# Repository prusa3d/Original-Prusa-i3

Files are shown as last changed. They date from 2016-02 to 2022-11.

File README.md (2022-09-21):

# Original Prusa i3 MK3S

Original Prusa i3 MK3S is a 3D printer project maintained by PRUSA RESEARCH.
Originates in [RepRap](https://reprap.org) project made possible by Dr. Adrian Bowyer and contributors.

This repository contains SCAD files and STLs of the printed parts.

**Links**

 * Prusa Research website : http://prusa3d.com
 * Product page: https://shop.prusa3d.com/en/3d-printers/180-original-prusa-i3-mk3-kit.html
 * Build manual: http://manual.prusa3d.com/c/Original_Prusa_i3_MK3_kit_assembly
 * Firmware : https://github.com/prusa3d/Prusa-Firmware
 * MK52 heatbed : https://github.com/prusa3d/Heatbed_MK52_magnetic
 * MK3 Power panic : https://github.com/prusa3d/MK3_Power_Panic
 * MK3S IR senzor : https://github.com/prusa3d/MKxS-IR-sensor

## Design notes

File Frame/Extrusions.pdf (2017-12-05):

## Profile

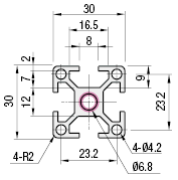
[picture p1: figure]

## Tapping

All 4.2 mm holes (both sides) tap 20 mm deep with M5

## Lengths

2x 205 mm : PAR-HWR-MK3-3030-205 2x 120 mm : PAR-HWR-MK3-3030-120

## Tolerance

+- 0.15 mm in length

# Material

Type: EN AC-51400-T5 Equiv. Surface finish: Black anodize

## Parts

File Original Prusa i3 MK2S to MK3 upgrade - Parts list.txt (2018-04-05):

Original Prusa i3 MK2S to Original Prusa i3 MK3 upgrade

Recommended print settings:
0.2 mm layer height, infill 20% GRID and material PETG.

Orange parts bundle (parts can be also printed in black):
X-end-motor (1x)	https://raw.githubusercontent.com/prusa3d/Original-Prusa-i3/MK3/Printed-Parts/stl/x-end-motor.stl
X-end-idler (1x)	https://raw.githubusercontent.com/prusa3d/Original-Prusa-i3/MK3/Printed-Parts/stl/x-end-idler.stl
Y-rod-holder (4x)	https://raw.githubusercontent.com/prusa3d/Original-Prusa-i3/MK3/Printed-Parts/stl/y-rod-holder.stl
Y-motor-holder (1x)	https://raw.githubusercontent.com/prusa3d/Original-Prusa-i3/MK3/Printed-Parts/stl/y-motor-holder.stl
Y-belt-holder (1x)	https://raw.githubusercontent.com/prusa3d/Original-Prusa-i3/MK3/Printed-Parts/stl/y-belt-holder.stl
Y-belt-idler (1x)	https://raw.githubusercontent.com/prusa3d/Original-Prusa-i3/MK3/Printed-Parts/stl/y-belt-idler.stl
Z-axis-top (1x) 	https://raw.githubusercontent.com/prusa3d/Original-Prusa-i3/MK3/Printed-Parts/stl/z-axis-top.stl
Z-axis-bottom (1x) 	https://raw.githubusercontent.com/prusa3d/Original-Prusa-i3/MK3/Printed-Parts/stl/z-axis-bottom.stl
LCD-supports (1x)	https://raw.githubusercontent.com/prusa3d/Original-Prusa-i3/MK3/Printed-Parts/stl/lcd-supports.stl

Black parts bundle (*extruder parts MUST BE printed in BLACK):
X-carriage* (1x)		https://raw.githubusercontent.com/prusa3d/Original-Prusa-i3/MK3/Printed-Parts/stl/x-carriage.stl
X-carriage-back* (1x)		https://raw.githubusercontent.com/prusa3d/Original-Prusa-i3/MK3/Printed-Parts/stl/x-carriage-back.stl     
Cable-holder* (1x)		https://raw.githubusercontent.com/prusa3d/Original-Prusa-i3/MK3/Printed-Parts/stl/cable-holder.stl
Extruder-body* (1x)		https://raw.githubusercontent.com/prusa3d/Original-Prusa-i3/MK3/Printed-Parts/stl/extruder-body.stl
Extruder-cover* (1x)		https://raw.githubusercontent.com/prusa3d/Original-Prusa-i3/MK3/Printed-Parts/stl/extruder-cover.stl
Extruder-idler-plug* (1x)	https://raw.githubusercontent.com/prusa3d/Original-Prusa-i3/MK3/Printed-Parts/stl/extruder-idler-plug.stl
Extruder-idler* (1x)		https://raw.githubusercontent.com/prusa3d/Original-Prusa-i3/MK3/Printed-Parts/stl/extruder-idler.stl
Filament-sensor-cover* (1x)	https://raw.githubusercontent.com/prusa3d/Original-Prusa-i3/MK3/Printed-Parts/stl/filament-sensor-cover.stl
Heatbed-cable-cover (1x)	https://raw.githubusercontent.com/prusa3d/Original-Prusa-i3/MK3/Printed-Parts/stl/heatbed-cable-cover.stl
Einsy-base (1x)			https://raw.githubusercontent.com/prusa3d/Original-Prusa-i3/MK3/Printed-Parts/stl/Einsy-base.stl
Einsy-doors (1x)		https://raw.githubusercontent.com/prusa3d/Original-Prusa-i3/MK3/Printed-Parts/stl/Einsy-doors.stl
Einsy-hinges (1x) 		https://raw.githubusercontent.com/prusa3d/Original-Prusa-i3/MK3/Printed-Parts/stl/Einsy-hinges.stl

License GNU GPL v3
https://www.prusa3d.com/prusa-i3-printable-parts/

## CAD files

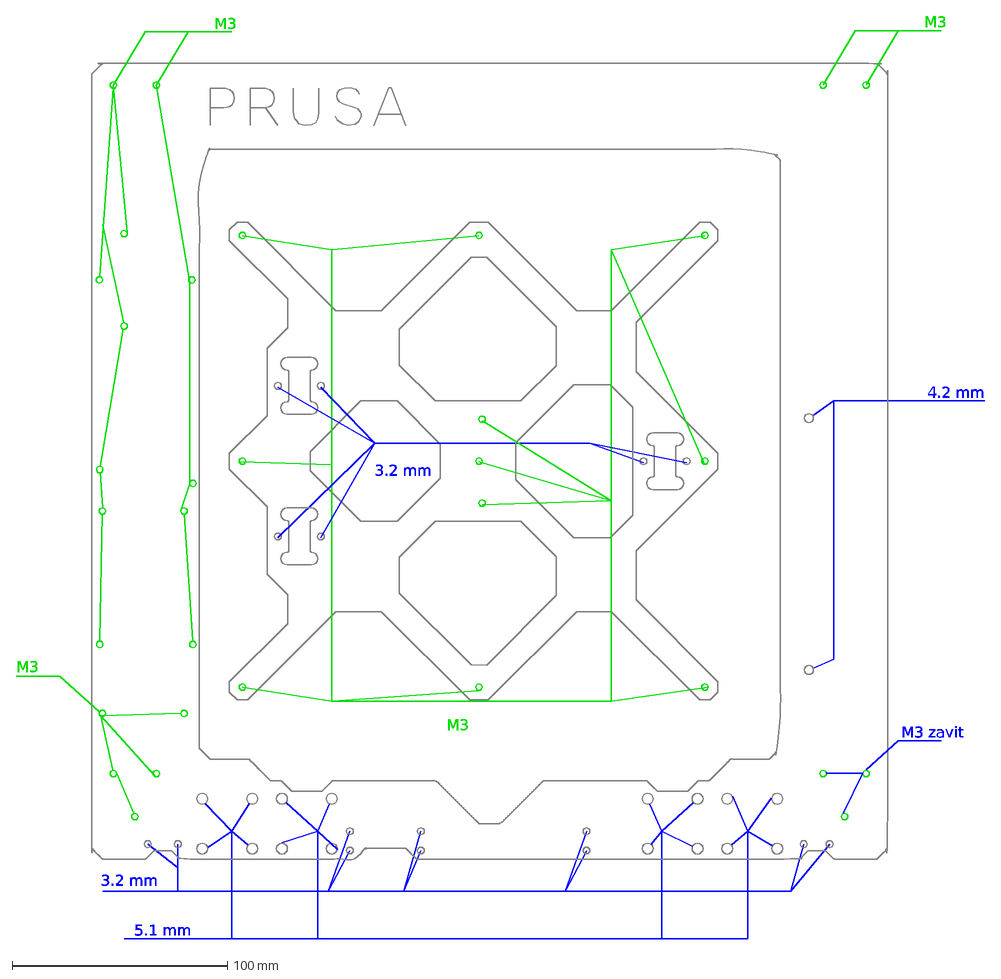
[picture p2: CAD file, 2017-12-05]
Frame/MK3v8b.dxf
4.2 mm
5.1 mm
M3
3.2 mm
M3 zavit

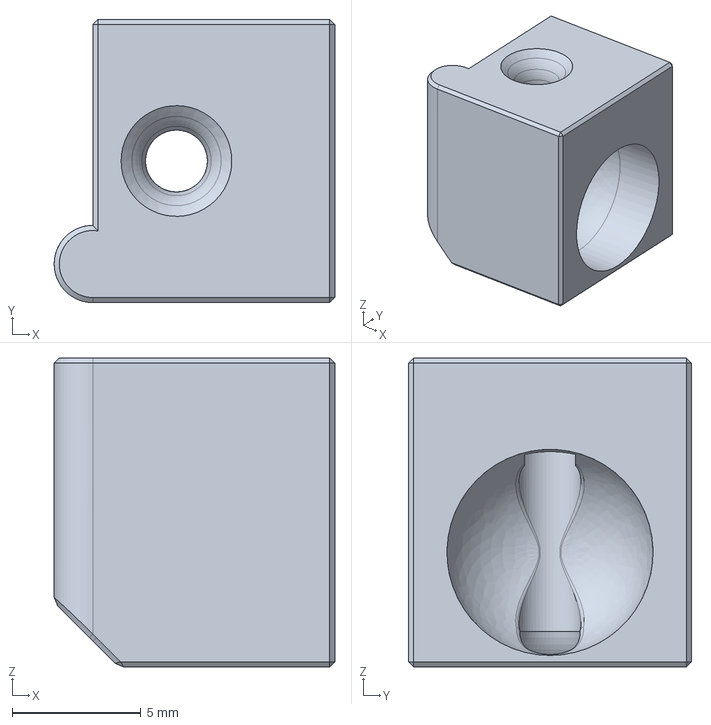
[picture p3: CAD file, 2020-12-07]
Printed-Parts/STEP/adapter-printer.stp
10.9 x 11.0 x 12.0 mm

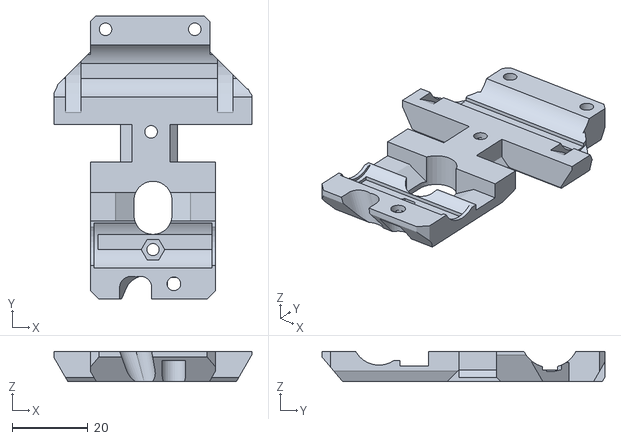
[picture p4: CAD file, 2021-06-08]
Printed-Parts/STL/x-carriage-back.stl
52.0 x 74.5 x 8.00

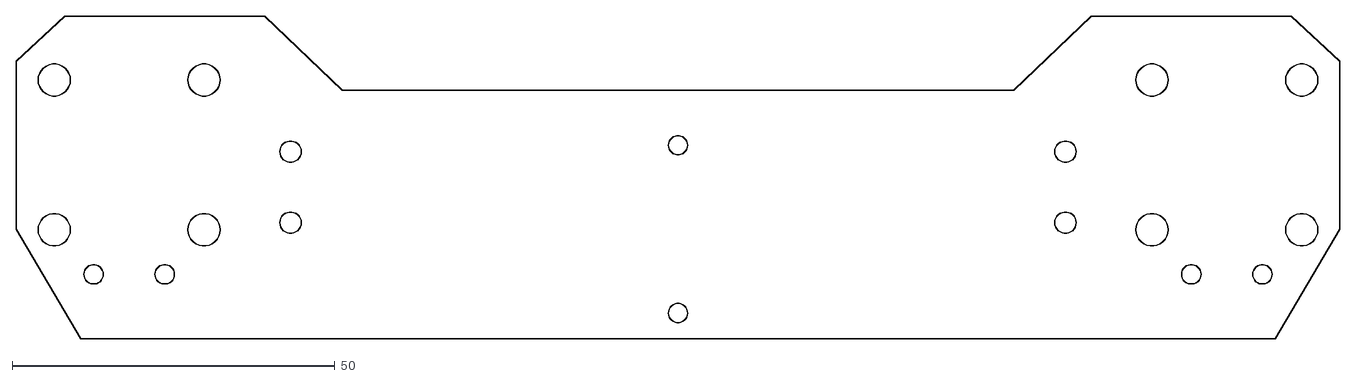
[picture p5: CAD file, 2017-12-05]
Frame/MK3-front-plate.dxf
205.0 x 50.0

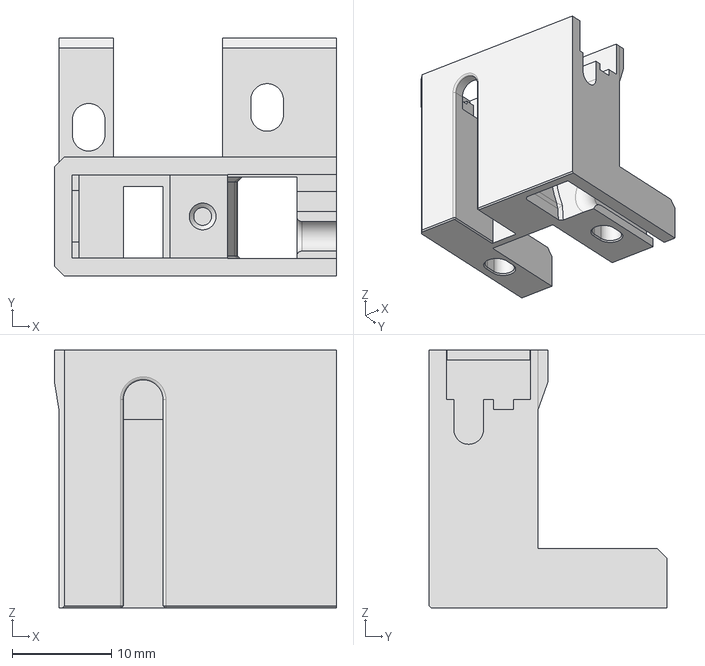
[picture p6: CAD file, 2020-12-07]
Printed-Parts/STEP/ir-sensor-holder-mmu2s.stp
28.5 x 24.0 x 26.0 mm

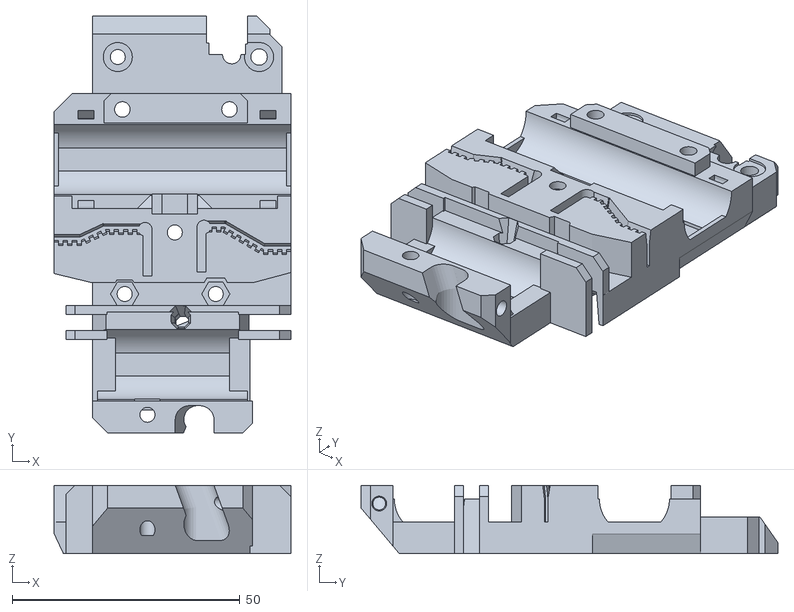
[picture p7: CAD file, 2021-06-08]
Printed-Parts/STL/x-carriage.stl
52.0 x 91.5 x 15.0

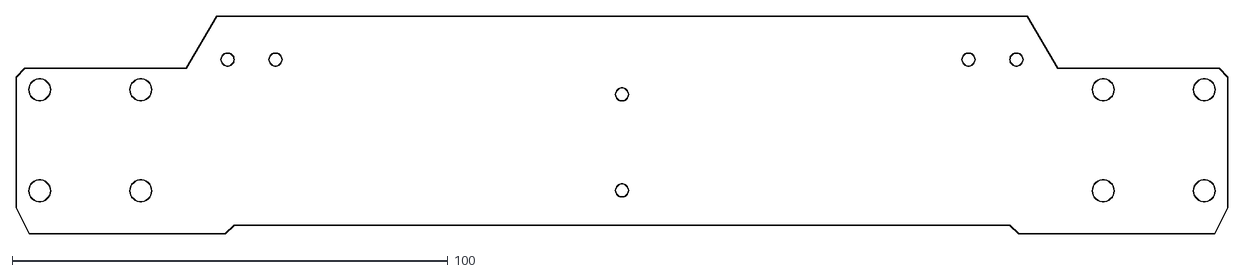
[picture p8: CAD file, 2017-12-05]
Frame/MK3-rear-plate.dxf
278.0 x 50.0

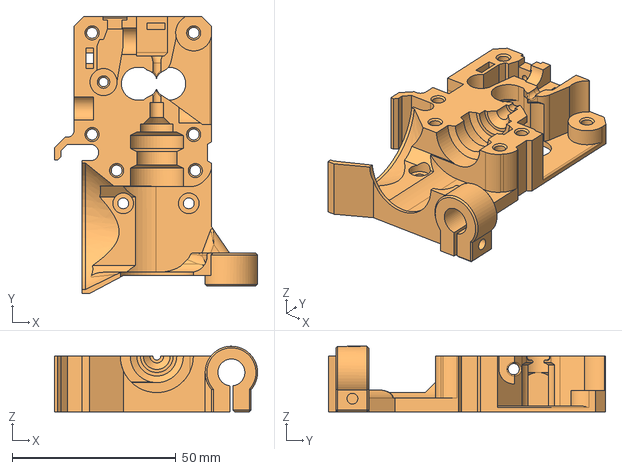
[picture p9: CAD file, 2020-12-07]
Printed-Parts/STEP/extruder-body.stp
62.0 x 84.5 x 20.0 mm

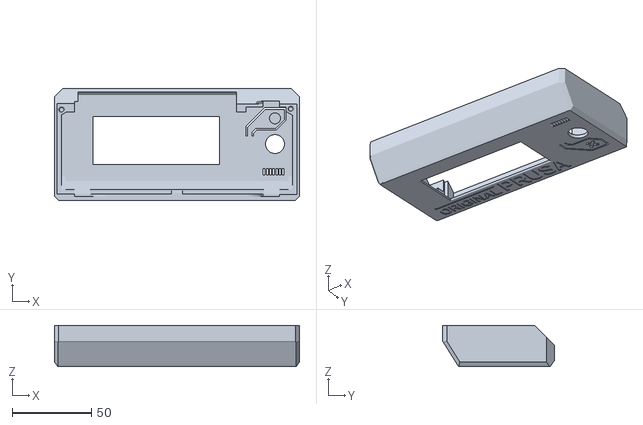
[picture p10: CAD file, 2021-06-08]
Printed-Parts/STL/LCD-cover-ORIGINAL-MK3.stl
155.0 x 70.7 x 26.0

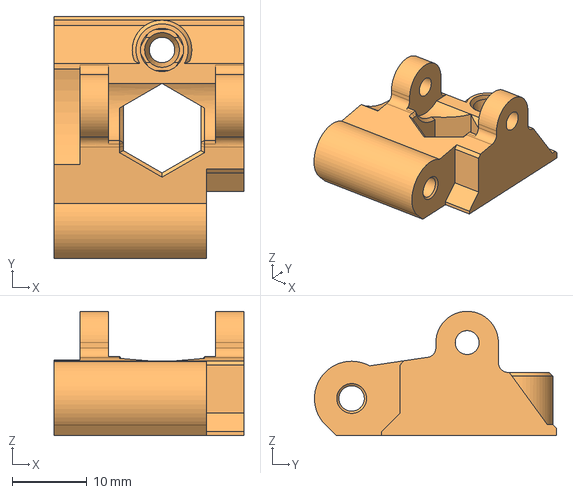
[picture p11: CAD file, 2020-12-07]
Printed-Parts/STEP/extruder-idler.stp
25.5 x 32.5 x 16.7 mm

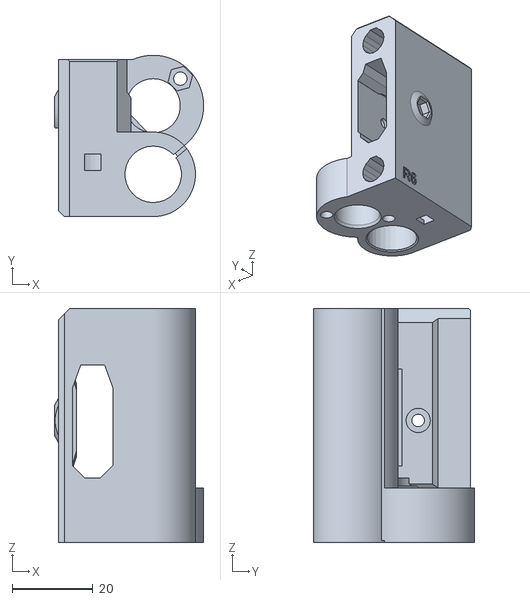
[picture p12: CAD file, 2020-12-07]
Printed-Parts/STL/x-end-idler.stl
37.0 x 40.0 x 58.0

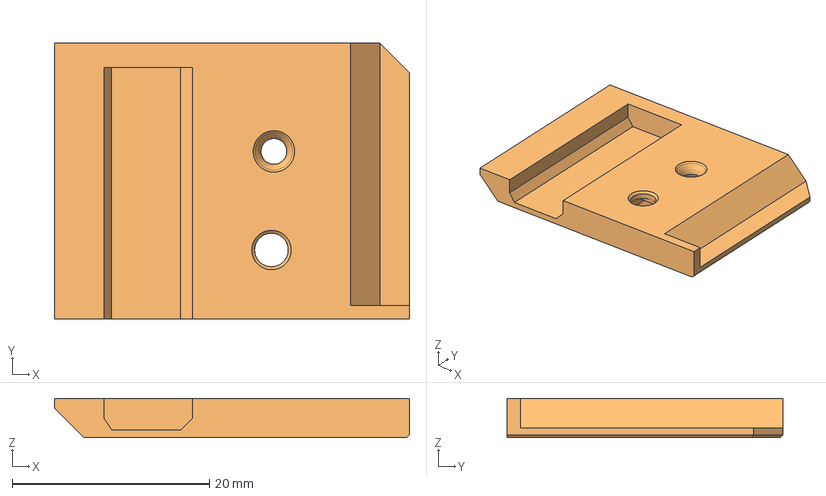
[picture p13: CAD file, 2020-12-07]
Printed-Parts/STEP/fs-cover.stp
36.0 x 28.0 x 4.00 mm

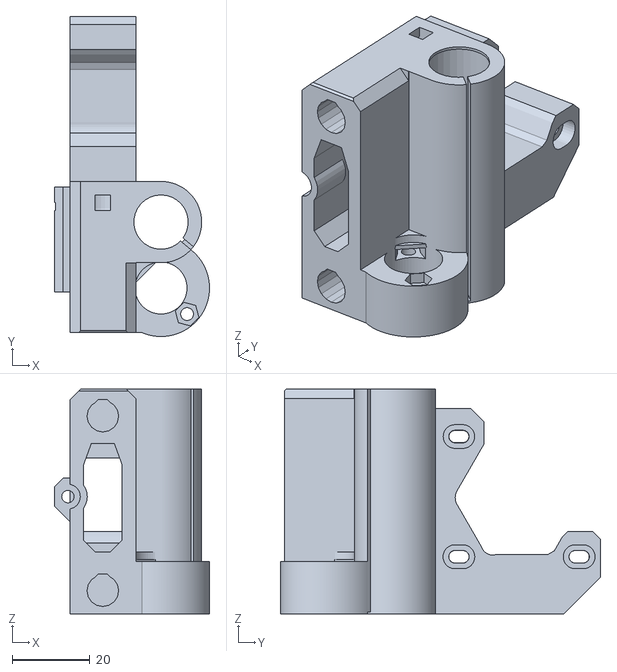
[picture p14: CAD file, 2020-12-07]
Printed-Parts/STL/x-end-motor.stl
40.0 x 82.5 x 58.0

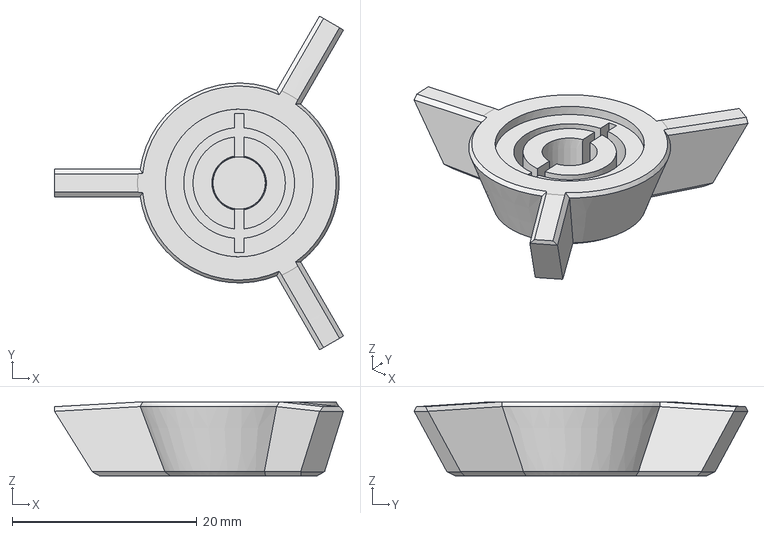
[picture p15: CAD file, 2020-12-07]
Printed-Parts/STEP/LCD-knob.stp
31.3 x 36.1 x 8.00 mm

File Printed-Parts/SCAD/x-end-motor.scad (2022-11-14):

// PRUSA iteration4
// X end motor
// GNU GPL v3
// Josef Průša <iam@josefprusa.cz> and contributors
// http://www.reprap.org/wiki/Prusa_Mendel
// http://prusamendel.org

use <x-end.scad>

module x_end_motor_base()
{
    x_end_base();
    translate(v=[-15,31,26.5]) cube(size = [17,44,53], center = true);

		
}

module x_end_motor_holes()
{
   x_end_holes();
    
    // Position to place
    translate(v=[-1,32,30.25])
    {
        // Belt hole
        translate(v=[-19,-21,-12]) cube(size = [10,25,22]);
        
        // Motor mounting holes

			for (x =[-1:0.25:1])
			{
        	translate(v=[0,-15.5+x,15.5]) rotate(a=[0,-90,0]) rotate(a=[0,0,90]) cylinder(h=30, r=1.55, $fn=60);
				translate(v=[0,-15.5+x,15.5]) rotate(a=[0,-90,0]) rotate(a=[0,0,90]) cylinder(h=18, r2=1.55, r1=1.7, $fn=60);
   	     translate(v=[1,-15.5+x,15.5]) rotate(a=[0,-90,0]) rotate(a=[0,0,90]) cylinder(h=10, r=3.05, $fn=60);
        
     	   	translate(v=[20,-15.5+x,-15.5]) rotate(a=[0,-90,0]) rotate(a=[0,0,90]) cylinder(h=70, r=1.6, $fn=30);
				translate(v=[0,-15.5+x,-15.5]) rotate(a=[0,-90,0]) rotate(a=[0,0,90]) cylinder(h=18, r2=1.55, r1=1.7, $fn=60);
     		  	translate(v=[1,-15.5+x,-15.5]) rotate(a=[0,-90,0]) rotate(a=[0,0,90]) cylinder(h=10, r=3.1, $fn=30);

	       	translate(v=[20,15.5+x,-15.5]) rotate(a=[0,-90,0]) rotate(a=[0,0,90]) cylinder(h=70, r=1.6, $fn=30);
				translate(v=[0,15.5+x,-15.5]) rotate(a=[0,-90,0]) rotate(a=[0,0,90]) cylinder(h=18, r2=1.55, r1=1.7, $fn=60);
   	     translate(v=[1,15.5+x,-15.5]) rotate(a=[0,-90,0]) rotate(a=[0,0,90]) cylinder(h=10, r=3.1, $fn=30);
     		};


        // Material saving cutout 
        translate(v=[-10,12,12]) cube(size = [60,42,42], center = true);
        translate(v=[-25,10.5,-11]) rotate([45,0,0]) cube(size = [60,10,10]);
        translate(v=[-25,21,-11]) rotate([45,0,0]) cube(size = [60,10,10]);

        // Material saving cutout
        translate(v=[-10,41,-30.5]) rotate(a=[45,0,0])  cube(size = [60,42,42], center = true);
        
        
        
    }

}

// Motor shaft cutout
module x_end_motor_shaft_cutout()
{
    union()
        {
        difference()
            {
            translate(v=[0,32,30]) rotate(a=[0,-90,0]) rotate(a=[0,0,90]) cylinder(h = 70, r=17, $fn=6);
            translate(v=[-10,-17+32,30]) cube(size = [60,2,10], center = true);
            translate(v=[-10,-8+32,-15.5+30]) rotate(a=[60,0,0]) cube(size = [60,2,10], center = true); 
            translate(v=[-10,8+32,-15.5+30]) rotate(a=[-60,0,0]) cube(size = [60,2,10], center = true);
            }
            translate(v=[-30,25.2,-11.8 +30]) rotate(a=[0,90,0]) cylinder(h = 30, r=3, $fn=30);
            translate(v=[-30,19.05,30]) rotate(a=[0,90,0]) cylinder(h = 30, r=3.5, $fn=100);
        }
}



   
  
    
   
// Final part
module x_end_motor()
{
    difference()
        {
            x_end_motor_base();
            x_end_motor_shaft_cutout();
            x_end_motor_holes();
       
            
            // waste pocket
            translate([-15,7,6]) rotate([90,0,0]) cylinder(h=3.5, r=5, $fn=30);   
            translate([-15,7,51]) rotate([90,0,0]) cylinder(h=3.5, r=5, $fn=30);   
            translate([-15,3.5,6]) rotate([90,0,0]) cylinder(h=3, r1=5, r2=4, $fn=30);   
            translate([-15,3.5,51]) rotate([90,0,0]) cylinder(h=3, r1=5, r2=4, $fn=30); 
          
            // rod contact window
            translate([-17,3,55]) cube([4,4,10]);
            translate([-17,3,-8]) cube([4,4,10]);
            translate([-30,-30,58]) cube([30,30,10]);
	                
            // version
            translate([-23.2,-20,2]) rotate([90,0,270]) linear_extrude(height = 0.6) 
            { text("R6",font = "helvetica:style=Bold", size=4, center=true); }   
            
        }

    translate([-15,10,6]) rotate([90,0,0]) cylinder(h=3, r=5, $fn=30);   
    translate([-15,10,51]) rotate([90,0,0]) cylinder(h=3, r=5, $fn=30);
 
    // bearing stop
    difference()
        {
            translate([0,0,57]) rotate([0,0,90]) cylinder( h=1, r=8, $fn=30);
            translate([0,0,56.9]) rotate([0,0,90]) cylinder( h=0.5, r1=8, r2=7,$fn=30);    
            translate([0,0,56.5]) rotate([0,0,90]) cylinder( h=2, r=7, $fn=30);
            translate([-0.18,-0.5,50]) rotate([0,0,-40]) cube([12,1,10]);
        }   
    
    // bearings spacer
    rotate([0,0,45]) difference()
    {
        translate([0,0,26]) rotate([0,0,90]) cylinder( h=6, r=8, $fn=30);
        translate([0,0,25]) rotate([0,0,90]) cylinder( h=8, r=7.55, $fn=60);    
        translate([0,0,25.9]) rotate([0,0,90]) cylinder( h=2, r2=7.5, r1=7.7,$fn=30);    
        translate([0,0,31.4]) rotate([0,0,90]) cylinder( h=2, r1=7.5, r2=8.3,$fn=30);    
        
        rotate([0,0,310]) translate([-2.5,0,26]) cube([5,15,10]);
        rotate([0,0,310-120]) translate([-2.5,0,26]) cube([5,15,10]);
        rotate([0,0,310-240]) translate([-2.5,0,26]) cube([5,15,10]);
    }
    
    // nut trap print suports
    
    	translate(v=[-5.8,-13.149,13.5]) rotate([0,0,45]) cube(size = [10,2.1,1], center = true);
    	translate(v=[-9.8,-11,13.7]) rotate([0,0,135]) cube(size = [8,2.1,0.4], center = true);
        
     translate(v=[-5.2,-8,13.7]) rotate([0,0,135]) cube(size = [8,2.1,0.4], center = true);
     translate(v=[-8.8,-8.55,13.5]) rotate([0,0,45]) cube(size = [8,2.1,1], center = true);
      
}

difference()
{
    union()
    {
        x_end_motor();
        translate([-8,-17,13.0]) rotate([0,0,44.7]) cube([10,1.5,1]);

		// belt tensioner body
				translate([-24,9,30.25]) rotate(a=[90,30,0]) cylinder(h=27, r=4, $fn=6);
				difference()
				{
					translate([-30,9-27,30.25]) rotate(a=[0,45,0]) cube([11,27,11]);
					translate([-37.465,9-27-1,20]) cube([10,30,21]);
					translate([-29,9-27-1,35]) cube([10,30,21]);
					translate([-20,9-27-1,20]) cube([25,30,21]);
				}
				difference()
				{
					translate([-24,-18,30.25]) rotate(a=[90,0,0]) cylinder(h=10.5, r=5, $fn=30);
					translate([-24-19.5,-18,20]) rotate(a=[90,0,0]) cube([20,20,20]);
				}

    }
    
    translate([-47,-40,60]) rotate([0,45,0]) cube([20,80,20]);    
    translate([-20,-30.5,69]) rotate([0,45,0]) cube([20,20,20]);    
    translate([-25,-37,49]) rotate([45,0,0]) cube([30,20,20]);   
    translate([-25,23.5,49]) rotate([45,0,0]) cube([30,20,20]);   


			// belt tensioner
		  translate(v=[0,32,30.25])
		    {
				translate([-24,-15.5-2.5,0]) rotate(a=[90,0,0]) cylinder(h=35, r=1.6, $fn=30);
				translate([-24,-15.5-4.5-30,0]) rotate(a=[90,0,0]) cylinder(h=30, r=3.2, $fn=30);
				translate([-24-10+2.8,-29,0-2.8]) cube([10,2.1,5.6]);
			 }
}   
    

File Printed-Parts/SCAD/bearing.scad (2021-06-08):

// PRUSA iteration3
// Bearing holders
// GNU GPL v3
// Josef Průša <iam@josefprusa.cz> and contributors
// http://www.reprap.org/wiki/Prusa_Mendel
// http://prusamendel.org

use <polyholes.scad>

bearing_diameter = 14.95;

module horizontal_bearing_base(bearings=1){
 translate(v=[0,0,6]) cube(size = [24,8+bearings*25,12], center = true);	
}

module horizontal_bearing_holes(bearings=1){
 cutter_lenght = 10+bearings*25;
 one_holder_lenght = 8+25;
 holder_lenght = 8+bearings*25;
 
 // Main bearing cut
 difference(){
  translate(v=[0,0,12]) rotate(a=[90,0,0]) translate(v=[0,0,-cutter_lenght/2]) cylinder(h = cutter_lenght, r=(bearing_diameter/2)+0.2, $fn=50);
  // Bearing retainers
  translate(v=[0,1-holder_lenght/2,3]) cube(size = [24,6,8], center = true);
  translate(v=[0,-1+holder_lenght/2,3]) cube(size = [24,6,8], center = true);
 }
 
 // Ziptie cutouts
 ziptie_cut_ofset = 0;
 for ( i = [0 : bearings-1] ){
  // For easier positioning I move them by half of one 
  // bearing holder then add each bearign lenght and then center again
  translate(v=[0,-holder_lenght/2,0]) translate(v=[0,one_holder_lenght/2+i*25,0]) difference(){
   union(){
    translate(v=[0,2-8.5,12]) rotate(a=[90,0,0]) translate(v=[0,0,0]) cylinder(h = 4, r=11.5, $fn=50);
    translate(v=[0,2+8.5,12]) rotate(a=[90,0,0]) translate(v=[0,0,0]) cylinder(h = 4, r=11.5, $fn=50);
   }
   translate(v=[0,12,12]) rotate(a=[90,0,0]) translate(v=[0,0,0]) cylinder(h = 24, r=9, $fn=50);
  }
 }
 
}
 
module horizontal_bearing_holes_nozip(bearings=1)
{
	cutter_lenght = 10+bearings*25;
	one_holder_lenght = 8+25;
	holder_lenght = 8+bearings*25;
 
	 // Main bearing cut
	 difference()
		{
		  	translate(v=[0,0,12]) rotate(a=[90,0,0]) translate(v=[0,0,-cutter_lenght/2]) cylinder(h = cutter_lenght, r=(bearing_diameter/2)+0.2, $fn=50);
			// Bearing retainers
			translate(v=[0,1-holder_lenght/2,3]) cube(size = [24,6,8], center = true);
			translate(v=[0,-1+holder_lenght/2,3]) cube(size = [24,6,8], center = true);
 		}
}

module horizontal_bearing_holes_nozip_smooth(bearings=1)
{
	cutter_lenght = 10+bearings*25;
	one_holder_lenght = 8+25;
	holder_lenght = 8+bearings*25;
 
	 // Main bearing cut
	 difference()
		{
		  	translate(v=[0,0,12]) rotate(a=[90,0,0]) translate(v=[0,0,-cutter_lenght/2]) cylinder(h = cutter_lenght, r=(bearing_diameter/2)+0.2, $fn=150);
			// Bearing retainers
			translate(v=[0,1-holder_lenght/2,3]) cube(size = [24,6,8], center = true);
			translate(v=[0,-1+holder_lenght/2,3]) cube(size = [24,6,8], center = true);
 		}
}

module horizontal_bearing_holes_smooth_nozip(bearings=1)
{
	cutter_lenght = 10+bearings*25;
	one_holder_lenght = 8+25;
	holder_lenght = 8+bearings*25;
 
	 // Main bearing cut
	 difference()
		{
		  	translate(v=[0,0,12]) rotate(a=[90,0,0]) translate(v=[0,0,-cutter_lenght/2]) cylinder(h = cutter_lenght, r=(bearing_diameter/2)+0.2, $fn=120);
			// Bearing retainers
			translate(v=[0,1-holder_lenght/2,3]) cube(size = [24,6,8], center = true);
			translate(v=[0,-1+holder_lenght/2,3]) cube(size = [24,6,8], center = true);
 		}
}




thinwall = 3;
bearing_size = bearing_diameter + 2 * thinwall;

module vertical_bearing_base(){
 translate(v=[-2-bearing_size/4,0,29]) cube(size = [4+bearing_size/2,bearing_size,58], center = true);
 cylinder(h = 58, r=bearing_size/2, $fn = 250);
}

module vertical_bearing_holes(){
  translate(v=[0,0,-1]) poly_cylinder(h = 62, r=(14.80/2));
  translate(v=[0,0,-0.1]) cylinder(r1=(bearing_diameter/2)+0.7,r2=(bearing_diameter/2), h=0.5);
  rotate(a=[0,0,-40]) translate(v=[bearing_diameter/2-2.9,-0.5,0.5]) cube(size = [thinwall*2,1,62]);

}

//difference(){
//vertical_bearing_base();
vertical_bearing_holes();
//}
//horizontal_bearing_test();
//horizontal_bearing_base(1);
//horizontal_bearing_holes(1);
//horizontal_bearing_holes_nozip(1);

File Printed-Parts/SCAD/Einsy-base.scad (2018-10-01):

// PRUSA iteration4
// Einsy base 
// GNU GPL v3
// Josef Průša <iam@josefprusa.cz> and contributors
// http://www.reprap.org/wiki/Prusa_Mendel
// http://prusamendel.org


module CubicPattern(Xdim, Ydim)
{
        for (x =[0:12:Xdim-10])
        {
            for (y =[0:12:Ydim-10])
            {
                translate([x,y,-0.2])cube([10,10,0.4]);
            }
        }
}

module BottomCubic()
{
    difference()
    {
        translate([5,5,0]) CubicPattern(110,90);
        translate([11,0,-1]) cube( [ 11, 40 , 4 ] );  
        translate([0,0,-1]) cube( [ 11, 28 , 4 ] );  
        translate([0,64,-1]) cube( [ 16, 28 , 4 ] ); 
        translate([95,64,-1]) cube( [ 20, 28 , 4 ] );  
        translate([95,0,-1]) cube( [ 20, 28 , 4 ] );  
        translate([76,-10,-1]) cube( [ 20, 20 , 4 ] );  
        translate([52,76,-1]) cube( [ 12, 20 , 4 ] );  
    }
}



// main body
module main_body()

         
{
      
    
       //raspberry frame
        
        
    
        // side panel
        cube( [ 118.5 , 92 , 2 ] );  

        // upper panel
        cube( [ 1.5 , 92 , 35 ] );  
        // rear panel
        translate( [ 0 , 90 , 0 ] ) cube( [ 105.5 , 2 , 35 ] );  
         

        // upper panel frame reinforcement
        translate( [ 0 , 0 , 1 ] ) cube( [ 5 , 7 , 34 ] );  

        // side panel reinforcement
       translate( [ 0 , 0 , 1 ] ) cube( [ 9 , 92 , 3 ] );  
        translate( [ 98 , 0 , 0 ] ) cube( [ 9 , 92 , 4 ] ); 
        
        // 
        translate([21,81,0]) cylinder( h = 4.5, r = 2.5, $fn=30);   
        translate([21+58,81,0]) cylinder( h = 4.5, r = 2.5, $fn=30);
      
        
        // ziptie cable managment
     translate( [0 , 55 , 22 ] )  difference() {
           
       translate( [0 , 0 , -2 ] ) cube( [ 5 , 8 , 10 ] );
       translate( [0 , -1 , -3 ] ) rotate([0,45,0])  cube( [ 5 , 10 , 8 ] );
       translate( [5, -1 , 6 ] ) rotate([0,-60,0])  cube( [ 5 , 10 , 8 ] );
      union() {  
       translate( [1.5 , 2.5 , 3.5] ) cube( [ 2 , 3 ,10 ] );
       translate( [3 , 2.5 , 2 ] ) cube( [ 5.5 , 3 ,2 ] );
       translate( [2 , 2.5 , 6.5 ] ) cube( [ 5 , 3 ,3 ] );
       
       difference () {    
       translate( [ 3 ,5.5 , 3.5 ] ) rotate([90,0,0]) cylinder( h = 3, r = 1.5, $fn=30);  
          translate( [3.5 , 1.5 , 4 ] ) cube( [ 5 , 5 ,3 ] );  
           
       }
       
       
       
       
        difference () {    
       translate( [ 4,5.5 , 4.5 ] ) rotate([90,0,0]) cylinder( h = 3, r = 1, $fn=30);      
       translate( [ 4,5.5 , 4.5 ] ) rotate([90,0,0]) cylinder( h = 3, r = 0.5, $fn=30);  
          translate( [3.5 , 1.5 , 4.5 ] ) cube( [ 5 , 5 ,3 ] );  
          translate( [4. , 1.5 , 4 ] ) cube( [ 5 , 5 ,3 ] ); 
       }
           }
     }
     
     translate( [25 , 91.5 , 22 ] ) rotate([0,0,-90])  difference() {
           
       translate( [0 , 0 , -2 ] ) cube( [ 5 , 8 , 10 ] );
       translate( [0 , -1 , -3 ] ) rotate([0,45,0])  cube( [ 5 , 10 , 8 ] );
       translate( [5, -1 , 6 ] ) rotate([0,-60,0])  cube( [ 5 , 10 , 8 ] );
      union() {  
       translate( [1.5 , 2.5 , 3.5] ) cube( [ 2 , 3 ,10 ] );
       translate( [3 , 2.5 , 2 ] ) cube( [ 5.5 , 3 ,2 ] );
       translate( [2 , 2.5 , 6.5 ] ) cube( [ 5 , 3 ,3 ] );
       
       difference () {    
       translate( [ 3 ,5.5 , 3.5 ] ) rotate([90,0,0]) cylinder( h = 3, r = 1.5, $fn=30);  
          translate( [3.5 , 1.5 , 4 ] ) cube( [ 5 , 5 ,3 ] );  
           
       }
       
       
       
       
        difference () {    
       translate( [ 4,5.5 , 4.5 ] ) rotate([90,0,0]) cylinder( h = 3, r = 1, $fn=30);      
       translate( [ 4,5.5 , 4.5 ] ) rotate([90,0,0]) cylinder( h = 3, r = 0.5, $fn=30);  
          translate( [3.5 , 1.5 , 4.5 ] ) cube( [ 5 , 5 ,3 ] );  
          translate( [4. , 1.5 , 4 ] ) cube( [ 5 , 5 ,3 ] ); 
       }
           }
     }
     
     
     
    difference()
        {
            // bottom side reinforcement    
            translate( [ 98 , 86 , 0 ] ) cube( [ 7.5 , 6 , 35 ] ); 
            translate( [ 96 , 79 , 0 ] ) rotate([0,0,45]) cube( [ 7.5 , 6 , 36 ] ); 
        }
        translate( [ 0 , 85 , 0 ] ) cube( [ 5.5 , 7 , 35 ] ); 

        // screw mounting block
        translate( [ 54 , 84 , 0 ] ) cube( [ 9.5 , 7 , 35 ] );  

        // frame side panel
        translate( [ 20 , 0 , 0 ] ) cube( [ 80 , 3 , 5 ] );  

        // Einsy mounting holes
        translate( [ 102.5 , 14 , 1 ] ) rotate([0,0,90]) cylinder( h = 7, r = 5.5, $fn=6); 
        translate( [ 102.5 , 75 , 1 ] ) rotate([0,0,90]) cylinder( h = 7, r = 5.5, $fn=6); 
        translate( [ 7.5 , 14 , 1 ] ) cylinder( h = 7, r = 5.5, $fn=6); 
        translate( [ 7.5 , 75 , 1 ] ) cylinder( h = 7, r = 5.5, $fn=6); 

        // corners reinforcement
        translate( [ 0 , 75 , 1 ] ) cube( [ 13 , 16 , 6 ] );  
        translate( [ 0 , 70.25 , 1 ] ) cube( [ 7.5 , 11 , 6 ] ); 
        translate( [ 0 , 7.75 , 1 ] ) cube( [ 7.5 , 11 , 6 ] ); 
        translate( [ 0 , 0 , 1 ] ) cube( [ 13 , 14 , 6 ] ); 

        // frame mounting screw blocks
        //upper
        translate( [ 1 , 0 , 0 ] ) cube( [ 28 , 4 , 10 ] );  
        translate( [ 18.45 , 0 , 0 ] ) cube( [ 3 , 4 , 5.5] ); 

        //lower
        translate( [ 98 , 0 , 0 ] ) cube( [ 20.5 , 4 , 10 ] ); 

       

        // door closing corner
        translate( [ 102 , 88.5 , 35 ] ) cylinder( h = 3, r1=2.5, r2=1, $fn=30);   

        // doors pin upper
        translate( [ 2 , 85 , 31 ] ) cube( [ 6 , 7 , 4] ); 
        translate( [ 4 , 88.5 , 35 ] ) cylinder( h = 3, r1=2.5, r2=1, $fn=30);   

        // x-axis cables entry hole body
        translate( [ 89 , 2 , 0 ] ) cylinder( h = 5, r = 6, $fn=6);   
        
       
}
    module rambo_popout_cover () {
        
        //raspberry cover
        translate( [ 20 , 37.5 , 0] )  cube( [ 3 , 1 , 0.5] );
        translate( [ 33 , 37.5 , 0] )  cube( [ 3 , 1 , 0.5] );
        translate( [ 45.8 , 37.5 , 0] )  cube( [ 3 , 1 , 0.5] );
        translate( [ 59 , 37.5 , 0] )  cube( [ 3 , 1 , 0.5] );
        translate( [72.5 , 37.5 , 0] )  cube( [ 3 , 1 , 0.5] );
        
        
        translate( [ 20 , 71.5 , 0] )  cube( [ 3 , 1 , 0.5] );
        translate( [ 33 , 71.5 , 0] )  cube( [ 3 , 1 , 0.5] );
        translate( [ 45.8 , 71.5 , 0] )  cube( [ 3 , 1 , 0.5] );
        translate( [ 59 , 71.5 , 0] )  cube( [ 3 , 1 , 0.5] );
        translate( [72.5 , 71.5 , 0] )  cube( [ 3 , 1 , 0.5] );
       
       
        translate( [ 9 , 51.5 , 0] )  cube( [ 5 , 7 , 0.5] );
        translate( [ 81 , 53.5 , 0] )  cube( [ 1 , 3 , 0.5] );
        
        
        
        
 
        
       difference() {
        translate( [ 14 , 38.5 , 0] )  cube( [ 67 , 33 , 2] );
        
           
        translate( [ 0.5 , 0.5 , 0] ) difference() 
           {   
        translate( [ 17.5 , 42 , -1.1] )  cylinder( h = 9.2, r = 8, $fn=40);
        translate( [ 17.2 , 41.7 , -1] )  cylinder( h = 9, r = 3.7, $fn=40);
        
        translate( [ 13.5 , 41.7 , -1] )  cube( [ 12.7 , 9 , 9] );
        translate( [ 17.2 , 38 , -1] )  cube( [ 9, 5 , 9] );     
  }  
  
  
        translate( [ 60 , 0 , 0] )  difference() 
           {   
        translate( [ 17.3 , 42.2 , -1.1] )  cylinder( h = 9.2, r = 8, $fn=40);
        translate( [ 17.3 , 42.2 , -1] )  cylinder( h = 9, r = 3.7, $fn=40);
        
        translate( [ 9.0 , 42 , -1] )  cube( [ 12 , 9 , 9] );
        translate( [ 8.8 , 38.5 , -1] )  cube( [ 9, 5 , 9] );   
             
}          
        translate( [ 60 , 26 , 0] )  difference() 
           {   
        translate( [ 17.3 , 41.8 , -1.1] )  cylinder( h = 9.2, r = 8, $fn=40);
        translate( [ 17.4 , 41.8 , -1] )  cylinder( h = 9, r = 3.7, $fn=40);
        
        translate( [ 8.5 , 33.5 , -1] )  cube( [ 9 , 12 , 9] );
        translate( [ 17 , 33 , -1] )  cube( [ 4, 9 , 9] ); 
}           
           
        translate( [ 0 , 26 , 0] )  difference() 
           {   
        translate( [ 17.7 , 41.8 , -1.1] )  cylinder( h = 9.2, r = 8, $fn=40);
        translate( [ 17.7 , 41.8 , -1] )  cylinder( h = 9, r = 3.7, $fn=40);
        
        translate( [ 17.5 , 33.5 , -1] )  cube( [ 9 , 12 , 9] );
        translate( [ 14 , 33.5 , -1] )  cube( [ 5, 9 , 9] );     
              }  }}



 
    module ventilation_holes()
    {
        
        difference () {
     for ( i = [-5 : 8] ){
      translate([46 + (i*5.5),10.5,-1]) cube([3.65,19+49.0,1.2]);
      translate([46 + (i*5.5),10.5,-1]) cube([3.65,18,10]);
      translate([46 + (i*5.5),10.5+25,-1]) cube([3.65,18,10]);
      translate([46 + (i*5.5),10.5+50,-1]) cube([3.65,18,10]);
    }
    difference () {
    translate( [ 13 , 35 , 0] )  cube( [ 71 , 39 , 2] );
    translate( [ 14 , 40.5 , -0.1] )  cube( [ 63 , 29 , 2.2] );
}}
}
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

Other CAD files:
Printed-Parts/STL/z-axis-bottom.stl
Printed-Parts/STEP/extruder-cover.stp
Printed-Parts/STL/heatbed-cable-cover.stl
Printed-Parts/STEP/fan-shroud.stp
Printed-Parts/SCAD/Einsy-doors.scad
Printed-Parts/SCAD/Einsy-hinges.scad
Printed-Parts/SCAD/Extruder-cable-clip.scad
Printed-Parts/SCAD/Heatbed-cable-clip.scad
Printed-Parts/SCAD/Heatbed-cable-clip_8mm.scad
Printed-Parts/SCAD/LCD-cover-ORIGINAL-MK3.scad
Printed-Parts/SCAD/PSU-cover-MK3.scad
Printed-Parts/SCAD/endstop-block.scad
Printed-Parts/SCAD/heatbed-cable-cover-clip.scad
Printed-Parts/SCAD/heatbed-cable-cover.scad
Printed-Parts/SCAD/lcd-supports.scad
Printed-Parts/SCAD/polyholes.scad
Printed-Parts/SCAD/print-fan-support.scad
Printed-Parts/SCAD/x-carriage-back.scad
Printed-Parts/SCAD/x-carriage.scad
Printed-Parts/SCAD/x-end-idler.scad
Printed-Parts/SCAD/x-end.scad
Printed-Parts/SCAD/z-axis-bottom.scad
Printed-Parts/SCAD/z-axis-top.scad
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

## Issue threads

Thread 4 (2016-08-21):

No scad files for LCD support a/b

ManuGithubSteam, 2016-08-21:
Hi

There is no scad file for the LCD-support "arms" a and b.

I would like to make a shorter version of the arms (shorter in length) so that the printer fits into the Ikea LACK enclosure (50cm max) but you have to make walls so you are left with 49 cm at best and that is not enough as the cables from the heatbed also need space.

In short, if you would make the lcd-support arms not so long and around 1cm shorter it would solve the issue. But as i can not find the scad files i can not attempt to do that myself.

Thanks
Manuel

akukan, 2016-08-22:
Files uploaded and available.

Closed 2016-08-22.

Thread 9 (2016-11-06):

Unable to preheat printer below 15 degrees C

StefanL2010, 2016-11-06:
PROBLEM:
If printer is started at an ambient temperature below 15 degrees Celsius it immediately triggers MINTEMP error on both the bed and hotend, even before any attempts to heat the bed or hotend.
This is because MINTEMP is set at 15 degrees in the firmware settings(usually 5 degrees on other printers). MINTEMP is a thermal runaway protection since a faulty thermistor usually sends a low value and should trigger a shutdown of the heater to prevent thermal runaway.
This also means that the printer can not be used at ambient temperatures below 15 degrees.

SUGGESTION:
No need to trigger MINTEMP error if the heater isn't enabled, thermal runaway isn't an issue when the heater is disabled.
When starting Preheat of the printer disable MINTEMP error for x amount of time to enable the bed and hotend to reach temperatures over 15 degrees.
Alternately add an option somewhere to trigger power to the bed and hotend for 10 seconds manually(overriding the MINTEMP error). That way you can manually add bursts of power to get the heat up.

Grogyan, 2016-11-06:
Or Just lower the threshold to something lower like 5 degrees C

StefanL2010, 2016-11-06:
Well, the question is if Prusa set it to 15 degrees for a reason or not. Perhaps they had some of their thermistors go bad and showing more than 5 degrees. If I just lower the MINTEMP without knowing this I could potentially risk a thermal runaway issue. The best way would be to still keep the 15 degree MINTEMP but still be able to preheat the printer.

Grogyan, 2016-11-06:
Are you sure you don't have a broken thermistor?

StefanL2010, 2016-11-06:
Yes, both the hotend and bed works perfectly. The MINTEMP is set at 15 degrees in Prusas firmware so it's only logical that the printer triggers a MINTEMP error below 15 degrees (since the printer is in a garage with an ambient temperature below 15 degrees). If anything it means the the termistors work as intended and are reading a correct temperature.
I'm looking for a workaround to be able to preheat the printer below 15 degrees even though the MINTEMP is set at 15 degrees.

prusa3d-bb, 2016-11-08:
I understand now :) We do suggest keeping the printer in the warm so that it avoids enviro factors like drafts and cold. I can link you to our firmware source files if you'd like to adjust them to a new setting.. I'd be very cautious about doing this. The other alternative would be to build an enclosure for your printer.

_________

Greyson Haswell
Prusa Research
Prague, Europe
info@prusa3d.com

--- original message ---
On Mon, Nov 7, 2016 at 12:01 am, <notifications@github.com> StefanL2010 wrote:

Yes, both the hotend and bed works perfectly. The MINTEMP is set at 15 degrees in Prusas firmware so it's only logical that the printer triggers a MINTEMP error below 15 degrees (since the printer is in a garage with an ambient temperature below 15 degrees). If anything it means the the termistors work as intended and are reading a correct temperature.
I'm looking for a workaround to be able to preheat the printer below 15 degrees even though the MINTEMP is set at 15 degrees.
—
You are receiving this because you are subscribed to this thread.
Reply to this email directly, view it on GitHub, or mute the thread.
--- end of original message ---

StefanL2010, 2016-11-08:
I can modify the firmware and change the MINTEM setting myself. But I'd rather not do that because it might be set to 15 degrees for a reason. Lowering the setting might cause thermal runaway issue. I already have the printer in an enclosure and the bed of the printer quickly heats up the enclosure. The problem is getting it going and starting the heater, once the heater is started the ambient temperature rises in the enclosure.
The FAQ at prusa3d.com states that the printer waits 45 seconds before triggering a MINTEMP error when the printer is operating (if a thermistor shows less than 15 degrees). The part that I consider a bug is that MITEMP error triggers directly when i power the printer on. There is no reason to trigger the MINTEMP error when the heaters are disabled.

bubnikv, 2016-11-08:
The thermistor reading range is set by a resistor divider at the RAMBO
board. At 15 degrees the voltage at the termistor is at its limit.
Therefore the RAMBO board cannot effectively measure lower temperatures
than what you read on the display.

The recommended workaround is to preheat the printer with a fan or a heat
gun. But be careful with a heat gun :-)

On Tue, Nov 8, 2016 at 9:07 AM, StefanL2010 <notifications@github.com>
wrote:

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

StefanL2010, 2016-11-08:
Well thats not true since the ambient temp around my printer was 5 degrees at startup last night and both the hotend and the bed both correctly read 5 degrees. So the thermistors have no problems reading lower values than 15 degrees. But thats missing the point.

1. The MINTEMP error is a thermal runaway protection only, Yes?
2. If Yes, why does the error trigger even though the heaters are not enabled?
3. The FAQ states there should be a 45 sec delay before MINTEMP triggers(if the temp is lower than 15 degrees). This is not true since it triggers directly at printer startup(even though heaters are not enabled).

prusa3d-bb, 2016-11-11:
Hello Stefan,

That's not entirely accurate. MINTEMP and Thermal runway can be related, but not always. If it's triggering right away, it can simply be a generic failure of the thermistor. In which case; send us a video of the instant flash up of the failure and we should be able to send you a replacement sent out to you on Monday after verification.

_________

Greyson Haswell
Prusa Research
Prague, Europe
info@prusa3d.com

--- original message ---
On Tue, Nov 8, 2016 at 12:41 pm, <notifications@github.com> StefanL2010 wrote:

Well thats not true since the ambient temp around my printer was 5 degrees at startup last night and both the hotend and the bed both correctly read 5 degrees. So the thermistors have no problems reading lower values than 15 degrees. But thats missing the point.
The MINTEMP error is a thermal runaway protection only, Yes?If Yes, why does the error trigger even though the heaters are not enabled?The FAQ states there should be a 45 sec delay before MINTEMP triggers(if the temp is lower than 15 degrees). This is not true since it triggers directly at printer startup(even though heaters are not enabled).
—
You are receiving this because you commented.
Reply to this email directly, view it on GitHub, or mute the thread.
--- end of original message ---

bardiir, 2017-07-17:
You can just grab the hotend nozzle for a few seconds until it gets over 15°C and then heat up normally from there. I wouldn't really change anything in the software, the limit is there for a reason anyway.

Closed 2017-12-05.

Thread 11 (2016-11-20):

Y motor holder a bit flimsy

pboschi, 2016-11-20:
The Y motor holder is a bit flimsy and bends, reducing tension and misaligning the belt. It should be integrated with the Y-distance part from the start, and come with 3 screw points instead of 2.

MartinMajewski, 2016-11-21:
Please take a look at my holder design on Thingiverse: http://www.thingiverse.com/thing:1837853

pboschi, 2016-11-21:
Thanks, i'll try that. The fact is that, depending on material and print quality, the additional bracket alone may or may not reduce the bending of the motor when the belt is finally installed and tightened. If not, you would still need the "Y-distance" part from this repository. With 3 brackets you could now install a damper, but the motor would be coupled to the rest of the printer by that "Y-distance" part, making the damper less effective.

I think that your design, slightly modified to be a bit wider (at least the lower "bracket"), would definitely solve the problem, and give the option to install a damper (with full effectiveness).

Just look at the X motor bracket... it doesn't bend at all because it has 3 screws AND it's wider.

MartinMajewski, 2016-11-21:
Please tell me what "Y-distance" part you mean exactly. I have searched the repository but I am not sure what you mean. Is it the 2-point Y-motor holder?

From my experience the 3-point motor holder is absolutely sufficient to hold the motor in position. I have printed it with PLA, three perimeters and 20% honeycomb infill and this is already overkill. But you can always print it sturdier.
The belt should never be that tight, that is bends the motor, anyway. It is absolutely enough if it does not slip over the pulley's teeth when you give it a firm pull. As soon as the motor starts bending (with a dampener or  without), you have tighten the belt too much. This puts unnecessary stress on the motor's shaft.

pboschi, 2016-11-21:
I'm referring to this part:
https://github.com/prusa3d/Original-Prusa-i3/blob/MK2/Printed-Parts/scad/Y-distance.scad

The belt is not over-tightened; but after some days of use i found a bending of the Y motor mount, which in turn causes the belt to slip on a side; that's a very minor problem i know, but with just some more width it would be perfect (but i'll just try with higher infill for now, as you suggested).
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

prusa3d-bb, 2016-11-24:
Hello,

It could possibly be resolved by extending the pulley on the shaft a little, so that it better aligns with the y-holder. It might help, while you're reprinting the part.

_________

Greyson Haswell
Prusa Research
Prague, Europe
info@prusa3d.com

--- original message ---
On Mon, Nov 21, 2016 at 11:40 pm, <notifications@github.com> pboschi wrote:

I'm referring to this part:
https://github.com/prusa3d/Original-Prusa-i3/blob/MK2/Printed-Parts/scad/Y-distance.scad
The belt is not over-tightened; but after some days of use i found a bending of the Y motor mount, which in turn causes the belt to slip on a side; that's a very minor problem i know, but with just some more width it would be perfect (but i'll just try with higher infill for now, as you suggested).

—
You are receiving this because you are subscribed to this thread.
Reply to this email directly, view it on GitHub, or mute the thread.
--- end of original message ---

pboschi, 2016-11-26:
These two things may help to fix the problem:
http://www.thingiverse.com/thing:1911701
http://www.thingiverse.com/thing:1914857

Prusa-Support, 2022-05-05:
This issue will be closed due to it being obsolete.

Marina Curzi
Prusa Research

Closed 2022-05-05.

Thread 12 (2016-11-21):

Printer allows unloading of filament below PLA melting temperature with no warning

mrjohnc, 2016-11-21:
I managed to clog my printer by accidentally pressing unload filament before the printer had reached the preheat temperature for the material I was using (PLA). This caused filament to get stuck in the nozzle further up and I had to take the print head apart to fix it.

Maybe add in a control to say only allow unload filament unload once printer has reached preheat temperature

I'm using 3.0.8

prusa3d-bb, 2016-11-22:
Hi John,

You can clean the hotend following those steps:
preheat the extruder to 260C and extrude some of the filament.
if extruding won't help, use the acupuncture needle and stick it up the nozzle from bottom.
the last option is to get a 1.5mm steel wire and insert it into the extruder instead of filament and then push it down.

Best regards

—
Dan Oravsky
Technical Support

PRUSA Research
+420 222 263 718
621/8a Prvniho pluku, 18600, Prague
shop.prusa3D.com

--- original message ---
On Mon, Nov 21, 2016 at 01:48 pm, <notifications@github.com> John Cummings wrote:

I managed to clog my printer by accidentally pressing unload filament before the printer had reached the preheat temperature for the material I was using (PLA). This caused filament to get stuck in the nozzle further up and I had to take the print head apart to fix it.
Maybe add in a control to say only allow unload filament unload once printer has reached preheat temperature
I'm using 3.0.8
—
You are receiving this because you are subscribed to this thread.
Reply to this email directly, view it on GitHub, or mute the thread.
--- end of original message ---

mrjohnc, 2016-11-22:
Hi Dan

I'm happy to say that I fixed the issue with help from Prusa support. My bug is related to the software issue that allowed this to happen. Its very easy to do by accident and takes quite a long time to fix the first time it happens.

Thanks

John

prusa3d-bb, 2016-11-23:
Hello John,

I just want to check that all is good now and you are able to print.

Let me know and have a nice day!

Monika Dostalova
Customer Support

PRUSA Research
+420 222 263 718
+421 220 570 305
621/8a Prvniho pluku, 18600, Prague
shop.prusa3D.com

--- original message ---
On Tue, Nov 22, 2016 at 05:11 pm, <notifications@github.com> John Cummings wrote:

Hi Dan
I'm happy to say that I fixed the issue with help from Prusa support. My bug is related to the software issue that allowed this to happen. Its very easy to do by accident and takes quite a long time to fix the first time it happens.
Thanks
John
—
You are receiving this because you commented.
Reply to this email directly, view it on GitHub, or mute the thread.
--- end of original message ---

mrjohnc, 2016-11-23:
Yes, absolutely fixed, I wasn't filing this about getting my printer fixed, just pointing out a software issue

Thanks

bardiir, 2017-07-17:
Actually I would like to see this as an advanced option to explicitly enable this to enable atomic pulls supported by the extruder motor instead of just yanking at the filament. Atomics are still the best way to get dirt out of the nozzle, although I'm pretty happy to say that I've managed to get over 100h print time already and not clog the nozzle yet thanks to the filament filter any taking care not to drop dirt into the feeder :)

mrjohnc, 2017-07-17:
> Actually I would like to see this as an advanced option to explicitly enable this to enable atomic pulls supported by the extruder motor instead of just yanking at the filament. Atomics are still the best way to get dirt out of the nozzle, although I'm pretty happy to say that I've managed to get over 100h print time already and not clog the nozzle yet thanks to the filament filter any taking care not to drop dirt into the feeder :)>

Yes this makes sense, to have it blocked when trying to unload filament normally when it is under temp and then a special option for atomic pull which would have an option for each filament type. The printer would then guide the user through the atomic pull process with clear instructions heating and cooling the hot end as needed.

Prusa-Support, 2022-05-05:
This issue will be closed due to it being obsolete.

Marina Curzi
Prusa Research

Closed 2022-05-05.

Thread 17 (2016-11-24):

Prevent oozing from the nozzle before calibration point check messing up your calibration

ManuGithubSteam, 2016-11-24:
Hello Prusa,

I noticed the following behavior:

When the nozzle heats up, the material is oozing out of the nozzle. This is normal due to heating. Note: I'm using the prusa profiles and material so everything should be ok in the temp. regard.

So before the 9 calibration recheck, i have to manually remove the oozed out filament to not mess up the calibration point recheck.

It would be easy i assume to put in a little gcode to wipe the nozzle a bit before the calibration recheck starts. Also a little retraction milli seconds before the calibration touches the bed will help. This way the ozzing while the check is minimised and the print is not messed up.

What do you think ?

Thanks!

pboschi, 2016-11-26:
i would change the default order of actions:
1) heat bed
2) 9-point calibration
3) go to 0,0,20 (so it's easy to clean manually)
4) heat nozzle
6) start

bubnikv, 2016-11-27:
The nozzle is hot at the time of the 9 point calibration intentionally. If
it was not hot, any leaked plastic at the tip of the nozzle would push the
bed from the probe making the calibration unreliable.

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

bardiir, 2017-07-17:
I'd suggest retracting a cm or so instead, this pulls out the filament from the hot zone and should prevent most of the oozing while measuring.

bubnikv, 2017-07-18:
> I'd suggest retracting a cm or so instead, this pulls out the filament
from the hot zone and should prevent most of the oozing while measuring.

At the start of the print, we don't know the position of the filament in
the melt zone. If you retract the filament out of the heat break, you may
clog the extruder by letting the molten filament expand where it should not
expand. This is exactly the issue all the single-extruder multi-material
setups face and we had to develop quite an extensive hardware / software
system to minimize the clogs to an acceptable level.

On Mon, Jul 17, 2017 at 6:08 PM, Alexander Faust <notifications@github.com>
wrote:

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

bardiir, 2017-07-18:
I'm currently not aroung the printer - can it physically move outside the bed with the nozzle? If so maybe do it like this:
Move outside bed perimenter
Extrude 5mm
Retract 5mm
Wait a few seconds
Wipe at the edge of the bed
Do calibration moves
Reinsert Filament 5mm
Prime & Print

If it can't move outside the bed perimeter maybe prime the nozzle on the right side of the bed first and then retract.
This way you don't have any risk of pulling out the filament too far as you insert it a controlled amount first, so if it wasn't in the wrong position to begin with it will not be in a wrong position afterwards.

fucx, 2017-07-18:
You could just do a retract before mesh bed levelling in your start gcode like the S3D config files by philipp.m on the forums: http://shop.prusa3d.com/forum/original-prusa-i3-mk2-f23/simplify3d-print-settings-august-30-2016--t938-s200.html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

He's running this start gcode which keeps the nozzle from oozing:

```
G28 W ; home all axes without mesh bed leveling
G1 F1000.0 ; set feed rate
G1 E-10 ; retract to avoid blobs on the bed
G80 ; run mesh bed leveling routine
G1 Y-3.0 ; prepare to prime
G1 E15 ; bring back the filament
G1 X60.0 E9.0 ; priming
G1 X100.0 E12.5 ; priming
```

bardiir, 2017-07-18:
@fucx This was my first idea too but as @bubnikv has explained, this could potentially clog the extruder as it uncontrolled pulls out the filament from an unknown position, so you need to establish a known position first or at least make sure you don't end up in a worse position than you started.

fucx, 2017-07-18:
@bardiir you're right. but keeping that in mind, it shouldn't be too much of a problem. it's not a general solution, of course. but if you're aware of the pitfalls, it should work.

bardiir, 2017-07-18:
@fucx yes but if there are any pitfalls it should not be included in the general Firmware of the printer to not cause any issues with inexperienced users. Advanced users can at any time manually add stuff like this to the slicer anyway. Blobs on the printbed don't cause prints to fail generally and the user should have the most stable solution possible at hand by default.

boelle, 2017-12-04:
i think this is more a cosmetic issue that a functional isuue... a few drops of filament should not matter

and as @bubnikv says it has to be hot or else filament that sits on the tip of nozzle will make the probing invalid

i think this one should be closed

Closed 2017-12-05.

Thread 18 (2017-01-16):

Extrusion Immediately After Color Change

lbussy, 2017-01-16:
When a color change is executed and you select "yes" to continue, the nozzle will immediately extrude ~40mm filament into mid-air and then move to the print.   I believe the offending section of GCode is this:

`M600`
`G1 E0.80000 F2100.00000`

I see no reason for the extrusion after the color change, and if one does not catch it and pull it off before printing resumes, the filament strand will embed in the print.

lbussy, 2017-01-16:
@cahe on Slack looked at this and found that the extrusion in GCode is there before and after.  He did find this portion of the firmware that seems likely on line 4494 of Marlin_main.cpp:

`//Not let's go back to print`

`     //Feed a little of filament to stabilize pressure`
`     target[E_AXIS]+= FILAMENTCHANGE_RECFEED;`
`     plan_buffer_line(target[X_AXIS], target[Y_AXIS], target[Z_AXIS], target[E_AXIS], FILAMENTCHANGE_EXFEED, active_extruder);`
`       `
`     //Retract`
`     target[E_AXIS]+= FILAMENTCHANGE_FIRSTRETRACT;`
`     plan_buffer_line(target[X_AXIS], target[Y_AXIS], target[Z_AXIS], target[E_AXIS], FILAMENTCHANGE_RFEED, active_extruder);`

This seems a likely culprit.  I'm not sure if this extra extrusion and then retraction is needed, or if something is causing it to extrude more than intended.

bubnikv, 2017-01-16:
The extra extrusion is intended. If you wait for a while to confirm that the filament has been exchanged successfully, some of the material may leak out of the nozzle, leading to a gap in a print. The extra extrusion has the purpose to pressurize the nozzle before resuming the print.

lbussy, 2017-01-16:
I can appreciate that a fresh extrusion may be desirable to pressurize the nozzle.  The practical issue however is that there is a piece of filament hanging off the nozzle as it goes to resume printing.  Without something like a "purge tower" to clean it, a user is left having to time cleaning the nozzle as it moves to print.

Have you personally tried color printing?  The experience will do more to understand the implications than I can hope to type here.   A low-height print makes it pretty difficult; it's possible someone might jam a tool (or worse a finger) against a hot print head while trying to clean that filament off.

lbussy, 2017-01-16:
@cahe mentioned something that made sense about that:  He suggested color change on infill - that would mitigate the impact of a gap.   If that is not possible, consider that it is typical to print the perimeter from the inside-out which would also mitigate any gap.

cahe, 2017-01-16:
I think I'd be super hard to detect when infill starts, since the script relays on Z values. A gap on the inner perimeter on the other hand doesn't seem that bad.

prusa3d-bb, 2017-01-17:
Hi there Maciej,

Could you please describe that a bit more? :)

Best regards

—
Tomáš Chvalina
Customer Support

PRUSA Research
+420 222 263 718
+421 220 570 305
621/8a Prvniho pluku, 18600, Prague
shop.prusa3D.com

--- original message ---
On Mon, Jan 16, 2017 at 06:18 pm, <notifications@github.com> Maciej Janowski wrote:

I think I'd be super hard to detect when infill starts, since the script relays on Z values. A gap on the inner perimeter on the other hand doesn't seem that bad.
—
You are receiving this because you are subscribed to this thread.
Reply to this email directly, view it on GitHub, or mute the thread.
--- end of original message ---

cahe, 2017-01-17:
@lbussy Can you provide us with some photos?

bubnikv, 2017-01-17:
I personally don't see this a big issue. I am using color print time to
time and after I confirm the filament change I just grab the excess thread
of material with tweezers. This way there is neither excess material nor a
gap on the printed object.

On Tue, Jan 17, 2017 at 4:18 PM, Maciej Janowski <notifications@github.com>
wrote:

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

lbussy, 2017-01-17:
I'll try to get photos/video if possible.

p3ck, 2017-05-11:
I find this annoying as well.  It has added a blob of extra filament on many prints of mine.  The print head is moving while it's extruding so it's very difficult to catch sometimes.

boelle, 2017-12-04:
since @lbussy & @p3ck  have the issue but not provided photos etc. i think its safe to say that this one is more or less solved and could be closed

domme81, 2019-02-06:
Same issure here. Just contacted the support because of that. After changing the color, just before the head moves back to the object it extrudes like one or two extra centimeters of filament in my case, that, if you don't try to catch it very fast, sticks somewhere to the object then...

And apart from that, a user option how much material is extruded before the "right color now?"-question would be fine. When using very different colors like black and white I often select "no" a few times to make sure the colors come perfectly clean out of the nozzle. But that would just be a nice-to-have. Thanks! :)

Enverex, 2019-03-01:
This is definitely still an issue and almost ruined one of my prints. After the filament swap, when you say OK to the change, it then squirts out 6cm or so of filament and travels to continue the print immediately (this was a low height print so actually getting to the nozzle was almost impossible).

I had to pause the print and try to pull the excess filament off the print itself (because it had already just embedded it) before letting it continue.

If you need help visualising this; Think of the filament change process, and then a split second before the head moves back to continue the print, it almost instantaneously squirts out a long thread of filament. There's no pause after this happens and it's not a slow extrude.

tracernz, 2019-03-02:
Yes, I saw that last time I did a filament change. Luckily managed to catch the string as it was travelling back to the print.

domme81, 2019-03-02:
My current ‘workaround’ is keeping the during the color change extruded material completely hanging out of the nozzle (not taking it off!), then hold it when it’s cool enough with one hand and THEN select OK to return to the print. That way the now falsely extruded filament is easier to catch because it will physically stick to the old one (that is still hanging there, which you already grabbed and hold). Might not work for everyone depending on the distance to the object the head has to travel and the amount of falsely extruded material. And a real fix would be very nice of course, but that helped me a bit for now saving some of my prints.

dsdimitrov, 2019-08-17:
Hit the same issue. Once it extrudes and asks if the color was changed successfully, I believe it should not extrude any further. What it does it extrudes some more material while moving to the printed object. This ruined two of my prints because I was not fast enough to catch it.

gogglespisano, 2020-05-17:
This is definitely still a problem and wasn't solved simply because no one provided a photo.  The comments made it clear it happens so fast and sometimes at such a low height it's very hard to get a photo.  I tried and failed.

The "pressurizing" reason for having this extra extrusion doesn't make sense if you proceed with printing immediately after the filament change.  Even after the extra extrusion, the head is still moved back over to the work area and a speed slow enough to have more filament ooze out.  Not really any different than the one second earlier when the filament change finished.

Please reopen this bug based on the continued examples and descriptions of the issue.  At the very least this should be configurable.

Area5142, 2020-05-18:
There is still a open issue in the Prusa-Firmware section: https://github.com/prusa3d/Prusa-Firmware/issues/2502
Where it is marked as a bug.

Closed 2017-12-05.

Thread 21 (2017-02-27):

Problems with extruder models

tkircher, 2017-02-27:
The extruder body and cover models both have issues where holes don't go all the way through. This is true of both the SCAD files and the generated STLs currently in the repository. Increasing the Z-axis lengths of the appropriate cylinders in extruder-main.scad solves these problems.

Also, the bearing support shaft, which fits into the extruder idler, doesn't exist in the repository. However, it did come included with the Prusa i3 mk2 kit and is an essential part. I'd be happy to provide patches for both of these issues.

Edit: There's also an issue with the y-corners SCAD and STL. Some fixes attached.
[prusa_fixes.zip](https://github.com/prusa3d/Original-Prusa-i3/files/820401/prusa_fixes.zip)

ryanneufeld, 2017-03-16:
This was done intentionally. Since you can't print circles in mid-air. Just use a 3mm drill-bit and clean out the holes

tkircher, 2017-03-18:
I had no trouble printing these on my Prusa. If you're having issues, it's better to print with a slightly tapered hole using a conical cutout than to require unnecessary post-processing. I've done that on several designs that had too much gap to bridge reliably, and cap screws still seat perfectly well.

ryanneufeld, 2017-03-18:
I am some explaining it. I am not even a contributor.

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

tkircher, 2017-03-18:
Normally I would just make my own fork, but the missing parts, at the very least, should get addressed here. There are other things like the reinforced Y stage motor mount that should probably also get included in the main repository.

akukan, 2017-12-05:
Explained, by design

Closed 2017-12-05.

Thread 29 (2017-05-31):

prusa super switch

JustinCaseOfWolf, 2017-05-31:
any plans to upload that?

JustinCaseOfWolf, 2017-06-01:
this one https://d17kynu4zpq5hy.cloudfront.net/igi/prusa3d/BMhgGmov5EBXZaxu.large

JustinCaseOfWolf, 2017-06-10:
anybody reading these messages?

madhunm, 2017-06-27:
+1 Any plans to upload the super switch schematic?

cscott, 2017-07-18:
Some small clues at https://github.com/MarlinFirmware/Marlin/commit/5b11b33854c9950b9a98005aa7783b1fe67b6269 FWIW.

AJMartel, 2017-09-14:
I am looking for the "MK42 stepper SWITCH rev 0.4" schematics as well.

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

JustinCaseOfWolf, 2017-09-14:
that is a very different design -fairly simple to gues swhat is going on there :)

JustinCaseOfWolf, 2017-10-27:
just to make it a bit clearer the circuit is so:
- assume A and B as being the 2 line inputs that can be either high or low
- C is A NOR B (through the 2 transistors circuit see http://www.electronics-tutorials.ws/logic/log46.gif for an example)  C will be high only when both A and B are low.
a relay has one control input, one controlled input and 2 output (normally open and normally closed). subject to control input being high or low we will see controlled input to either normally open or normally closed outputs.
basic diagram:
                     / output when control input is high
control input -- controlled input
                     \ output when control input is low

the 3 relays are defined as such:

    / M1 ( this will be power when both A and B are low)
C  - power
    \ FWD1 (this will output power when either A or B or both are high)

    / FWD2 (this will be power when A is high which makes C low)
A  - FWD1 (this will be power in when either A or B or both are high) (this is output on low from C relay)
    \ M2 (this will be power when A is low and B is high - we need C low)

    / M3 (this will be power when A and B are high which makes C low)
B  - FWD2 (this will be power in when A is high which makes C low) (this is output on high from A relay)
    \ M4 (this will be power when A is high and B is low which makes C low)

in plain english:
 -first relay will control a motor(1) when both inputs are low, otherwise will forward the current to second relay.
 -second relay will forward current to third relay when first input is high or control a motor(2) when second input is high. if second input is low then first relay is active. and second relay doesnt have current
 -third relay will output power to a motor(3) when second input is high or to a motor(4) when second input is low. third relay only has power when first input is high, otherwise it will not give current to any motors.

hope this helps.

ok1hra, 2017-10-27:
Source now available here https://github.com/prusa3d/MK2mm_Stepper_switch

bubnikv, 2017-10-27:
Documentation has been provided. Closing this issue.

boelle, 2017-12-04:
@bubnikv i think you forgot to hit the close button, there are also these other issues that could be closed

https://github.com/prusa3d/Original-Prusa-i3/issues/32
https://github.com/prusa3d/Original-Prusa-i3/issues/30
https://github.com/prusa3d/Original-Prusa-i3/issues/28
https://github.com/prusa3d/Original-Prusa-i3/issues/21
https://github.com/prusa3d/Original-Prusa-i3/issues/18
https://github.com/prusa3d/Original-Prusa-i3/issues/17
https://github.com/prusa3d/Original-Prusa-i3/issues/13
https://github.com/prusa3d/Original-Prusa-i3/issues/10
https://github.com/prusa3d/Original-Prusa-i3/issues/9
https://github.com/prusa3d/Original-Prusa-i3/issues/6
https://github.com/prusa3d/Original-Prusa-i3/issues/1

These ones you might want to pay some attention on

https://github.com/prusa3d/Original-Prusa-i3/issues/16
https://github.com/prusa3d/Original-Prusa-i3/issues/12
https://github.com/prusa3d/Original-Prusa-i3/issues/11
https://github.com/prusa3d/Original-Prusa-i3/issues/8

bubnikv, 2017-12-04:
@boelle Thanks for your efforts. I am more on the Slic3r side of the development, it is up to @michalprusa @akukan @ok1hra to close the HW related issues.

boelle, 2017-12-04:
@bubnikv  @michalprusa @akukan @ok1hra

no problem, since the isue list was so short i read them all and a lot of them did not make sense to keep open anymore. On a few of the issues i have made a comment on why i think they can be closed

boelle, 2017-12-05:
@akukan  thanks for cleaning up a bit

i made this list of issues that could be closed and you got a few

#32
#30
#28
#21
#18
#17
#13
#10
#9
#6
#1

akukan, 2017-12-05:
@boelle thanks for help, for the rest of the issues some work needs to be done so this will take little bit more time.

boelle, 2017-12-05:
@akukan no problemo

currently i'm looking at the DXF's for the MK3, they are not 100% perfect

i have started to make comments in https://github.com/prusa3d/Original-Prusa-i3/pull/36

is that the best place leave comments for mk3 ?

Closed 2017-12-05.

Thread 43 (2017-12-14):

Missing MK2.5 RAMBo cover hinges?

gregsaun, 2017-12-14:
Hi Prusa team,

I was checking the new RAMBo covers that comes with MK2.5, looks like a nice "hidden" update! The new door is 2mm thinner (18mm instead of 20mm on MK2s) and the top hinge hole looks a bit different. I was then surprised to not see new hinges for MK2.5, are they missing?

akukan, 2017-12-14:
Stl file was missing, updated :-)

Closed 2017-12-14.

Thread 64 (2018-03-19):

MK3 extruder idler shaft holes are too tight

gregsaun, 2018-03-19:
During the build of my MK2.5 I had the same issue as lot of other users, impossible to put the shaft in.

I suggest to use same technique as pushfit_rod module from x-ends.scad for this hole.

prusa3d-bb, 2018-03-21:
Hello,

Sorry to hear you are also experiencing the same issue and thanks for your suggestion on the GitHub page.

Have you been able to solve it?

Regards,

—
Blas Palencia
Customer Support

PRUSA Research
+420 222 263 718
+421 220 570 305
188/7a Partyzánská, 17000, Prague
shop.prusa3D.com

Please rate our reply ...be generous :-)

--- original message ---
On Mon, Mar 19, 2018 at 11:32 am, <notifications@github.com> Grégoire Saunier wrote:

During the build of my MK2.5 I had the same issue as lot of other users, impossible to put the shaft in.

I suggest to use same technique as pushfit_rod module from x-ends.scad for this hole.

—

You are receiving this because you are subscribed to this thread.

Reply to this email directly, view it on GitHub, or mute the thread.
--- end of original message ---

gregsaun, 2018-03-21:
Yes I use a file to increase hole

prusa3d-bb, 2018-03-23:
Hello,

Very happy to hear :)

Nice weekend!

—
Blas Palencia
Customer Support

PRUSA Research
+420 222 263 718
+421 220 570 305
188/7a Partyzánská, 17000, Prague
shop.prusa3D.com

Please rate our reply ...be generous :-)

--- original message ---
On Wed, Mar 21, 2018 at 09:44 am, <notifications@github.com> Grégoire Saunier wrote:

Yes I use a file to increase hole

—

You are receiving this because you commented.

Reply to this email directly, view it on GitHub, or mute the thread.
--- end of original message ---

gregsaun, 2018-03-23:
Hope you will fix this for other users 😉

ManuGithubSteam, 2018-05-05:
Just to let you know there is a report on the prusa build pages, that after heavy use for two months, this hole in the idler got wider and printing was not possible anymore because the pressure was too low on the filament. So I'm not sure making it wider is a good solution. But I also do not have another good one...

prusa3d-bb, 2018-05-08:
Hello,

We know about these report but it is only happening to a small quantity of customers.

Please let me know if the issue gets worse and you need our help. You can always try to print a new part.

https://www.prusa3d.com/prusa-i3-printable-parts/

Regards,

—
Blas Palencia
Customer Support

PRUSA Research
+420 222 263 718
+421 220 570 305
188/7a Partyzánská, 17000, Prague
shop.prusa3D.com

Please rate our reply ...be generous :-)

--- original message ---
On Sat, May 5, 2018 at 08:25 am, <notifications@github.com> Manuel wrote:

Just to let you know there is a report on the prusa build pages, that after heavy use for two months, this hole in the idler got wider and printing was not possible anymore because the pressure was too low on the filament. So I'm not sure making it wider is a good solution. But I also do not have another good one...

—

You are receiving this because you commented.

Reply to this email directly, view it on GitHub, or mute the thread.
--- end of original message ---

Prusa-Support, 2022-05-10:
If you are still having issues with the extruder idler please contact us at info@prusa3d.com.

Marina Curzi
Prusa Research

Closed 2022-05-10.

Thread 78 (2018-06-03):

MK3 Stops in the middle of prints for a filament change. I didn't tell the print to have a filament change.

derekaward, 2018-06-03:
Firmware: 3.2.1-576

It started when a print I downloaded a file from thingiverse.com [https://www.thingiverse.com/make:496393].

Imported it to prusa control. Then started printing, it wanted to do a filament change after the second layer. This was the first time it happened to me so I didn't cancel the print and I went through the process of changing the filament. It did a filament change 7 times!

I thought it might have been the file but no I looked and the gcode and it didn't have M600 to start the process.

I finished the print and started another one... Didn't have to change filament during that print.

I print a few more things and none of them needed a filament change.

Today i'm printing a vase, i'm attaching the gcode [here](https://drive.google.com/open?id=1slHa2pS3rzEfpV6WC2nNYZJPOUz-X2gf). (Using Slic3r)

This time I had to go thought the process twice. I posted on the Pursa Owner FB page and someone told me to turn off the filament sensor. I did and the print right now is still going with out stopping.

I really hope this is an oversight on my part.

derekaward, 2018-06-03:
I found the code that was getting injected. The artic

derekaward, 2018-06-03:
Keeping it open just in case.

tracernz, 2018-06-03:
This happens when the filament sensor doesn't detect the filament moving. Presumably the idea is to unload the filament, cut the (jamming) end off, and put it back in to continue. Unfortunately I have also had a few false positives from this.

derekaward, 2018-06-03:
Thanks for the feedback! Before it went to bed last night I read somewhere that a person was having the same issue and it was because they were using transparent filament. I was using transparent filament both times this accrued. I hope there will be an update to change the wording, so it doesn't sound like you mess something up in the slicer.

kris82, 2018-07-02:
I've experienced a similar issue few times. If everything goes fine after that it is just annoying but it can happen that this is actually the end of your printing. So far (I just have a printer for a week now) the issue had the following consequences:

First when that has happened (I guess as my wife heard the same "beeps") I was away and couldn't do nothing. When I get back I've noticed information on LCD stating something about timeout and temperature (idle for too long while extruder and bed heated?)
 After this error / information there was no possibility to resume print so 20 hours of printing time was lost... I was printing https://www.thingiverse.com/thing:2901274

It has happened again today for me after printing for around half an hour of simple model. I've unloaded PLA and loaded it again but temperatures were too low when it has started to print so again printing went directly to bin..

I've restarted the same code and this time everything was fine up to the end without asking for a fillament change.

In both of these cases I was using red PLA on MK3 with firmware 3.2.1-576

prusa3d-bb, 2018-07-03:
Hello,

I believe the filament sensor is giving false lectures and stopping the printer. It happens when the filament has bright or transparent colors. There are 2 things you can do:

- Disable the filament sensor while printing this materials.

- Download and install the latest Firmware just released yesterday and that improve the sensor performance.

https://www.prusa3d.com/drivers/

Can you please provide me the order number of your kit/printer?

—
Blas Palencia
Customer Support

PRUSA Research
+420 222 263 718
+421 220 570 305
188/7a Partyzánská, 17000, Prague
shop.prusa3D.com

Please rate our reply ...be generous :-)

--- original message ---
On Mon, Jul 2, 2018 at 10:49 pm, <notifications@github.com> kris82 wrote:

I've experienced a similar issue few times. If everything goes fine after that it is just annoying but it can happen that this is actually the end of your printing. So far (I just have a printer for a week now) the issue had the following consequences:

First when that has happened (I guess as my wife heard the same "beeps") I was away and couldn't do nothing. When I get back I've noticed information on LCD stating something about timeout and temperature (idle for too long while extruder and bed heated?)

After this error / information there was no possibility to resume print so 20 hours of printing time was lost... I was printing https://www.thingiverse.com/thing:2901274

It has happened again today for me after printing for around half an hour of simple model. I've unloaded PLA and loaded it again but temperatures were too low when it has started to print so again printing went directly to bin..

I've restarted the same code and this time everything was fine up to the end without asking for a fillament change.

In both of these cases I was using red PLA on MK3 with firmware 3.2.1-576

—

You are receiving this because you are subscribed to this thread.

Reply to this email directly, view it on GitHub, or mute the thread.
--- end of original message ---

kris82, 2018-07-03:
Hi,

You are absolutely right, I've spent yesterday some time to analyse the source code and I can't see any any other possibility than getting a false positives from sensor.

Currently I've disabled the sensor before some better solution will be available. I'll try a new firmware tomorrow when another of my long print will finish and new trapezoid nut arrive.

Generally despite of possible issue with sensor I think it would be great to add an option to resume printing after heating is stopped for security.

 I'll take a closer look at code today as it was quite late yesterday

My order number is: 182132700.

prusa3d-bb, 2018-07-09:
Hello,

Yes, let me know how is going. Also, thanks for feedback and I will add your suggestion to our 'customer wishes' list.

Regards,

—
Blas Palencia
Customer Support

PRUSA Research
+420 222 263 718
+421 220 570 305
188/7a Partyzánská, 17000, Prague
shop.prusa3D.com

Please rate our reply ...be generous :-)

--- original message ---
On Tue, Jul 3, 2018 at 12:37 pm, <notifications@github.com> kris82 wrote:

Hi,

You are absolutely right, I've spent yesterday some time to analyse the source code and I can't see any any other possibility than getting a false positives from sensor.

Currently I've disabled the sensor before some better solution will be available. I'll try a new firmware tomorrow when another of my long print will finish and new trapezoid nut arrive.

Generally despite of possible issue with sensor I think it would be great to add an option to resume printing after heating is stopped for security.

I'll take a closer look at code today as it was quite late yesterday

My order number is: 182132700.

—

You are receiving this because you commented.

Reply to this email directly, view it on GitHub, or mute the thread.
--- end of original message ---

dpmurphy, 2018-08-27:
I received my mk3 a week or so ago. I’ve started printing with esun petg and I see this fail at least every 30 mins. Half the prints are failures....and this is with latest downloaded today firmware.
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
ManuGithubSteam, 2018-11-15:
Hi,

Black Filament ist to glossy. The Devs know about this and the newest fw
should improve the detection.

But I just disable the filament sensor while printing very glossy
filament...

Hope this helps..

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

harrysamuel, 2018-12-18:
Just face it the Prusa I3 Mk3 was a mistake.  Wish I bought another cheap XYZ printer, never should have sold my first 3 printers. over 4,000 hours and no pause, pause, pause, pause. They ran all night every night.

JohnCoker, 2019-01-10:
I see this same problem with Prusa white PLA and firmware 3.5.1. Turning off the filament sensor allowed me to get through the print without stopping.

LolHens, 2019-01-10:
I've always had this problem with TPU, so I applied this small modification to my i3 and now it works perfectly:
https://www.thingiverse.com/thing:3129921
No pauses no matter what filament.

crashtest22, 2019-01-19:
Have had pausing issue today and was with a new Filament so I did some searching...I am having pause with sainsmart TPU in black...no other TPU has done this and its the only black filament I have

nahuelcarou, 2019-07-25:
@prusa3d-bb , I have also the same problem "stops in the middle of the print and asks for a filament change". Using Transparent PLA from OWL.

Order Reference from my Prusa MK3s KIT: 192304150

I hope I get some positive feedback from Prusa. Not just deactivating the sensor.

Thanks in advance,

Nahuel Carou
nahuel.carou@gmail.com

aanelli, 2019-09-24:
Kind of a weird thing, but I'm getting this with my ender 3 pro, which doesn't even have a filament sensor

darBis, 2019-09-24:
@prusa3d-bb if you have MK3S, this exact reported issue is not same as yours. MK3S has a different type of filament sensor, that is not sensitive to filament properties. If you have a first variant of the sensor, a "lever with a tower poking up", you could try readjusting the filament sensor according to a manual that arrived with your printer. Try if it solves the issue. It is a little bit fiddly setup and needs to be adjusted correctly.

ldboehm, 2020-01-19:
This happened to me today.
It is work with a semitransparent filament...believe it or not...it is.
It is definitely tied to the filament sensor and/or autoloading.
When I turn those off the issue goes away.

nahuelcarou, 2020-01-19:
Hi, try to calibrate better your filament sensor. If not, try to modify the mechanism for a better one. For example the one with comes with the mmu2 is more robust than the original one withouth the mmu2.

OutlawAndy, 2020-01-19:
This issue is resolved by the **mk3s** extruder upgrade.  Therefore, it should probably be closed.

On a side note, Github is really designed to handle this sort of thing automatically.
*i.e. auto closing resolved issues via commit message reference.*

*e.g. commit message that would automatically link to, and close this issue:*

    Fixed (#78)

Besides just the obvious time savings for the repo maintainers, using Github’s built in issue handling provides users documentation and a link trail they can follow to help them understand how an issue was resolved and what they need to do in order to benefit from the fix.

kic883, 2020-02-06:
I have assembled my MK3S since last week and I encoutered this issue this morning in the middle of a 10 hours print. This is not my first print (probably 10th) but this is the first time I use non Prusa brand PLA.  At first I thought I add color change by mistake, but I check there is no M600 commend in my gcode.

The PLA that I was using is a rainbow color PLA, not sure whether this will affect the filament sensor.

cbr600, 2020-04-13:
I just started having this on my MK2S. It is the first time using Black ABS and it happens always after printing the nozzle clean line after Z calibration at the beginning of a print. I was also just starting to use the latest firmware and Slic3r. I went to Slic3r 2.2.0+ to eliminate the wait for hours for preview that I get from PrusaControl. But I was also getting problem feeding.  The extruder was indeed empty. Going to back to PrusaControl fixed that problem. I’m 18 hours into a 26 hour print without issue.

3d-gussner, 2020-04-14:
@cbr600 I am not sure if this is the correct repository to report your issue.
Maybe https://github.com/prusa3d/Prusa-Firmware or https://github.com/prusa3d/PrusaSlicer are a better place for that.

3d-gussner, 2024-01-04:
@daddyfixit Please reopen you issue in the Prusa-Firmware repository https://github.com/prusa3d/Prusa-Firmware as this is for the parts.

Tie-fighter, 2025-07-04:
I am also affected by this on my MK3S 😭
I am unsure if it is the filament sensor, but either way, the on-screen information is misleading, as it states M600 as the reason.
Slicer and Firmware are up to date.

Closed 2025-08-02.

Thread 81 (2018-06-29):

MK3 heat break has step that accumulates filament and causes jams

matthew-humphrey, 2018-06-29:
The Prusa-designed E3D heat break on i3 MK3 printers has a "step" inside the tube. This step extrusion problems including jams and broken filament.

See the attached photo for a picture from a microscope of my heat break. The area in focus is some Prusa translucent green PETG that has accumulated in the step. This contamination was causing jams and poor print quality. I was unable to remove it even with repeated cold pulls.

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

Crunch69, 2018-06-29:
that explains the jams I keep having isnt the e3d heatbreak suppose to be smooth that is what they advertise

Zaf9670, 2018-06-29:
I have my heat break apart at home. I will take a look to see if mine has the same knot.

c-stewart, 2018-06-29:
Correct me if I'm wrong but I believe that Prusa gets custom heartbreaks
from E3D that include this difference, to be compatible with the multi
material upgrade.

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

murphy2712, 2018-06-29:
I believe it was only necessary for MMU v1, which is retired now.

c-stewart, 2018-06-29:
Right, but it wasn't when they started shipping mk3's. So the question is,
is this the same thing or something different?

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

Zaf9670, 2018-06-30:
I did not notice the step/knot in my heatbreak but I may have needed more light. I just got done replacing my heatbreak with the E3D Titanium.

matthew-humphrey, 2018-06-30:
It looks like the heatbreaks they are shipping now no longer have the problem. Many of us who got printers earlier do have this issue, though.

Crunch69, 2018-07-01:
when did prusa switch back to the stock e3d heat break?

matthew-humphrey, 2018-07-01:
I don't know if it's stock or just correctly machined not to have that step. I can confirm that replacing the Prusa HB with a genuine E3D resolved my issue.

ThaliaFromPrussia, 2018-08-04:
At which height is the step? Where the PTFE tube ends in the heat sink or where the heatsink and the nozzle come together?
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

matthew-humphrey, 2018-08-04:
It's actually right in the middle of the heatbreak. micro-swiss heatbreak has one as well, by the way.

Closed 2018-08-04.

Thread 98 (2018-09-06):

Filament Runout sensor?

npgoalkeeper, 2018-09-06:
Instead of using a PINDA probe or an optical laser to detect filament, why not use a wheel and 2 bearings with a magnetic encoder such as an AS5047P to detect the filament? It can detect speed and the presence of the filament easily, as long as its moving. This shouldn't matter with any of the printer's functions.

Moorviper, 2018-09-06:
Then you have to set the  wheel for each filament.
the laser is a good way.
I am currently building my own multimaterial device (uses 2 laser mouse sensor and detect in addition the filament by color by another sensor.
It also checks under the nozzle if the color is clean and then wipe the nozzle  with a brush.
Then i need no purge tower or wipe into infill on my printers.

ManuGithubSteam, 2018-09-06:
I sencond the laser :-)

npgoalkeeper, 2018-09-07:
Why does it need to be set for each filament? It can be like other printers, using a spring-loaded idler gear. As long as the wheel spins and matches the desired extrusion rate, it should be okay. I don't see how the as5047p (not the as5601 lol) would react any different to a flexible than PLA.

npgoalkeeper, 2018-09-07:
The only thing I do see, however, is the cost. It is heavier and costs 10x as much for this setup rather than a laser. Also, lasers throw out false positives.

Moorviper, 2018-09-07:
I got two prusa laser sensor clones for around 5€ inkl shipping i don't think you are getting much cheaper.
The cheapest magnetic encoder on digikey is around 4,5€ alone

bdynamic, 2018-09-07:
@Moorviper Could you maybe share your source? Ali has them for about 11$...

jltx1, 2018-09-09:
My fix:
https://www.thingiverse.com/thing:3091625 <https://www.thingiverse.com/thing:3091625>

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

npgoalkeeper, 2018-09-14:
That defeats the point of why I opened this issue, however. The PINDA probe cant detect jams.

Closed 2018-11-23.

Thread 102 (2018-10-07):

MMU Pulley Body Model Error

tbedore, 2018-10-07:
I sliced the file in Slic3r and it has all these lines in the model which are then reflected in the print making it weak, see attached photo
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

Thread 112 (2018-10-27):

MK3, extruder fan part, append hook on the right side

mariusvw, 2018-10-27:
Sometimes it happens that the cooling part does not fit straight, adding a little hook on the richt site to clip it on will help supporting it to be straight.

(already working on this, will soon make PR)

mariusvw, 2018-10-29:
Hello Marina,

It is not a problem caused with the ordered parts, it occurs when printing your own parts.
Since the right side (left in the picture) has no attaching to the extruder body it "hangs" a bit more.
When you look closely you see that it is slightly not at te same level compared to both sides.

![Uploading IMG_0824.jpg…]()

Adding a little "hook" to the fan part will force it to stay in place, you still have one bolt on the left side to lock it in place.

You can see my idea more as an upgrade than as a problem.

Almost finished the change so I will be adding a pull request referring to this issue soon.

-Marius

prusa3d-bb, 2018-10-30:
Hello,

Thank you for your email. Unfortunately I could not open the picture.

Best regards,

—
Marina Curzi
Customer Support

PRUSA Research
+420 222 263 718
+421 220 570 305
188/7a Partyzánská, 17000, Prague
shop.prusa3D.com

For simple troubleshooting, please use: http://help.prusa3d.com

Please rate our reply ...be generous :-)

--- original message ---
On Mon, Oct 29, 2018 at 08:29 pm, <notifications@github.com> Marius van Witzenburg wrote:

Hello Marina,

It is not a problem caused with the ordered parts, it occurs when printing your own parts.

Since the right side (left in the picture) has no attaching to the extruder body it "hangs" a bit more.

When you look closely you see that it is slightly not at te same level compared to both sides.

Adding a little "hook" to the fan part will force it to stay in place, you still have one bolt on the left side to lock it in place.

You can see my idea more as an upgrade than as a problem.

Almost finished the change so I will be adding a pull request referring to this issue soon.

-Marius

—

You are receiving this because you commented.

Reply to this email directly, view it on GitHub, or mute the thread.
--- end of original message ---

rrauenza, 2018-10-31:
I believe what @mariusvw is saying is that because the parts cooler nozzle is only screwed in with one screw, and that screw is only on one side, the parts cooler tends to hang a little at an angle.  I've also have seen this.

mariusvw, 2018-11-01:
@prusa3d-bb what @rrauenza describes is exactly what I am trying to say.

I almost finished an upgrade for this on the SCAD files, will make a PR.

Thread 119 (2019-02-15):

The current MK3S extruder body is 0.4 mm loose(r)

3Delights, 2019-02-15:
The user **jonnieZG** over on the Prusa Forum is reporting that: _The current MK3S extruder body is 0.4 mm loose(r)_ and that it might be a good idea to change this as it is causing the extruder to wiggle.

Please see this forum topic:
[https://shop.prusa3d.com/forum/general-discussion-announcements-and-releases-f69/the-current-mk3s-extruder-body-is-0-4-mm-loose-r--t27757.html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](
https://shop.prusa3d.com/forum/general-discussion-announcements-and-releases-f69/the-current-mk3s-extruder-body-is-0-4-mm-loose-r--t27757.html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)

jonnieZG, 2019-03-06:
Another user also pointed out that it would be good to change the neck grip tolerances from +0.2 mm to 0.1 mm, so the neck socket diameters would be 16.1 mm and 12.1 mm. I added that to my mod here https://www.thingiverse.com/thing:3428292, but it might be a good idea to make the change on the official model too.

tstoegi, 2020-07-08:
Still no comment or recommendation from Prusa yet?

jonnieZG, 2020-12-10:
This issue is fixed in R6, as all tolerances are set to the values proposed here. R6 introduces also some other improvements, so we can close this issue as solved.

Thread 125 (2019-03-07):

hardware stops heating waiting for inserts... operator asleep 17 hour print... I need to continue the print... how?

carterm2, 2019-03-07:
Prusa I3 Mk3 3.6.0
Latest Slicr3

I am trying to find out how to finish the last 5% of a print after a heater stop... please read to find out the situation.

...
In Slic3r Prusa... I added an M600 to my print, with the plus button....

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

I inserted the recommended text, from another Prusa Forum Post...

https://shop.prusa3d.com/forum/others-archive--f82/pause-print-in-gcode-t2034.html#p125758

 in a text editor... inplace of M600

M300 ;ACTIVATE BEEPER
G1 X10.000 Y200.000; parking position GET THE PRUSA TO STICK IT'S TONGUE OUT!
M1; user stop
G28 Y
M105; return to current temp

This stops the print, beeps, moves the extruder to the back left side of the printed, sets up a resume/cancel button on my OctoPrint screen, rehomes Y, and is supposed to....

Return to print temperature.

But I was asleep, and the printer turned of the heat for safety... I forgot the error message on the Prusa Screen

Q1
How can I start the print for the last 5%... Homing Z with the Panda probe will knock the part off the bed...

Q2
Can I replace the M600 text with my own in Slic3r?

Thanks,

Carter

tobymurray, 2019-05-21:
This repo is for the printer parts - I imagine you'll find a bit more traction on https://github.com/prusa3d/Prusa-Firmware (the repo for the software that actually executes on the printer).

Prusa-Support, 2022-05-16:
Since this issue is over 3 years old now and actually doesn't belong to this repo, I will be closing it now.

Marek Micek
Prusa Research

Closed 2022-05-16.

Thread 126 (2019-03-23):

GCodes for MMU2S printed parts reset my printer

acorderob, 2019-03-23:
The gcodes provided at https://www.prusa3d.com/prusa-i3-printable-parts/ for the MMU2 to MMU2S upgrade (for the MK3) reset my printer just after mesh bed leveling.

I'm using FW 3.6.0.

This happened with these gcode files:

- MK3S_extruder_part1_PET_8H30MIN.gcode
- MK3S_extruder_part2_PET_1H30MIN.gcode
- MMU2S_MK3S_S_BUFFER_PET_9H15MM.gcode

This is the start of one of them:

```gcode
M73 P0 R523
M73 Q0 S528
M201 X1000 Y1000 Z1000 E5000 ; sets maximum accelerations, mm/sec^2
M203 X200 Y200 Z12 E120 ; sets maximum feedrates, mm/sec
M204 P1250 R1250 T1250 ; sets acceleration (P, T) and retract acceleration (R), mm/sec^2
M205 X8.00 Y8.00 Z0.40 E1.50 ; sets the jerk limits, mm/sec
M205 S0 T0 ; sets the minimum extruding and travel feed rate, mm/sec
M107
M115 U3.5.1 ; tell printer latest fw version
M83  ; extruder relative mode
M104 S230 ; set extruder temp
M140 S85 ; set bed temp
M190 S85 ; wait for bed temp
M109 S230 ; wait for extruder temp
G28 W ; home all without mesh bed level
G80 ; mesh bed leveling
G1 Y-3.0 F1000.0 ; go outside print area
G92 E0.0
G1 X60.0 E9.0  F1000.0 ; intro line

```
The last thing that i know it runs is the mesh bed leveling (G80). Then it just resets without starting the intro line. I don't see anything wrong with the gcode.

Slicing the stls myself worked fine and i could print them.

For comparison, this is the start of my slicing that worked. Most of it is the same.

```gcode
M73 P0 R303
M73 Q0 S305
M201 X1000 Y1000 Z1000 E5000 ; sets maximum accelerations, mm/sec^2
M203 X200 Y200 Z12 E120 ; sets maximum feedrates, mm/sec
M204 P1250 R1250 T1250 ; sets acceleration (P, T) and retract acceleration (R), mm/sec^2
M205 X8.00 Y8.00 Z0.40 E1.50 ; sets the jerk limits, mm/sec
M205 S0 T0 ; sets the minimum extruding and travel feed rate, mm/sec
M107
M107 ; Fan off
M83  ; Extruder relative mode
G21 ; Set units to millimeters
G90 ; Use absolute coordinates
M220 S100 ; speed factor 100%
Tx ; choose filament

G28 W ; Home all without mesh bed level

M140 S85 ; Set bed temp
M109 S200 ; Set extruder temp before bed level
M190 S85 ; Wait for bed temp

M860 S35 ; Wait for pinda temp

G80 ; Mesh bed leveling

M109 S230 ; Wait for extruder temp

; Go outside print area
G1 Y-3.0 F1000.0
G1 Z0.4 F1000.0

Tc ; load filament

; Purge line
G1 X55.0 E8.0 F2000.0

```

thadude3, 2019-06-25:
I am randomly seeing this issue too. Was working fine then just started resetting right at the priming phase.

tdub415, 2019-07-01:
I'm also getting resets after the mesh level when it should be priming on some files.

tdub415, 2019-07-01:
Though it seems to happen only when I'm using gcode sliced in a non prusa slicer, operating in single mode, when filament isn't loaded to nozzle.  The same files that reset when I try running them with filament not loaded to nozzle seem to work fine when filament is loaded to nozzle prior to starting.  I am also printing via Octoprint, rather than SD card.

nnarc, 2019-07-02:
Having the same issue with firmware v3.7.2 using gcode for the prusa enclosure v2 found here: https://www.prusaprinters.org/prints/3673-mmu2s-enclosure

Have a MK3S with MMU2S, using SD.

Project381, 2019-07-12:
I also have this issue, when filament is not preloaded to nozzle the printer will reset after calibration has completed. It happened with v3.7.1 and now with 3.7.2. The printer would also also reset when spool join was turned on and the filament ran out, this seems to have been resolved since updating to 3.7.2.

bornhaeusser, 2019-08-16:
This happens to me too 3.7.2 - i run in this problem since i activated SpoolJoin on.
I deactivated it and maual load it into nossel. Then Print was starting normal.

Closed 2023-05-14.

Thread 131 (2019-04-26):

MMU2S pulley body not strong enough

tobymurray, 2019-04-26:
The selector of the MMU2S currently homes against the "left" (non-motor) side of the [mmu2-pulley-body](https://github.com/prusa3d/Original-Prusa-i3/blob/MMU2/STL/mmu2-pulley-body.stl). As I received it from Prusa, it's simply not strong enough. When the selector homes (by ramming into the side) the left side flexes enough that it causes a misalignment of the selector and the PTFE tubes that feed the selector.
I confirmed this by hand, first by turning off the printer and manually turning the selector screw until the filament could slip through (confirming it was the selector blocking it), and secondly by holding the pulley body upright with my hand when the selector initially homes. Both of these yielded a well-positioned selector.
Not really sure if this is a design flaw or implementation flaw (not printing with enough perimeters to hold it rigid), but either way it is a pain.

Nailig, 2019-05-01:
I seem to have the same problem. I already found remakes on thingiverse which widen the hole towards the finda sensor to try to solve this problem. But perhaps that is not the best solution.

xiphmont, 2019-07-20:
The firmware, as written, is not intended to home to the left.  It's trying to home to the right and watch for a motor stall.  All that back and forth before it goes left (or in some cases just jagged left movement)?  That's it looking for the right stop and not finding because the process is unfortunately buggy and terminating erroneously due to driver stutters.  The 'ramming the left stop' is a result of that.  OTOH, it's also something of a failsafe in that it sort of works, and gets the job done most of the time.

I *think* I know why this is happening, but I need more testing to be sure. Unfortunately, it requires some amount of firmware surgery, so it's a simple fix but not a tiny patch...

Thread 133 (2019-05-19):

Hotend wires get damaged due wrong cable-holder

mariusvw, 2019-05-19:
Lately I got a several MK3 upgrades in service, it happens they all run into the problem where the hotend wires get too low and hit the heatbed cover bolt where the bolt-end is facing up.

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

Here someone already started a discussion about this with a good photo showing what happens.

https://www.reddit.com/r/3Dprinting/comments/b9dxhc/just_noticed_that_the_red_wire_coming_out_of_the/

Again, I am willing to help developing on improvements. Just need the right files and workflow.

austinvojta, 2019-05-19:
Simple modification, I have changed the heatbed cable cover to use the problematic screw flipped around. So now you put a nut on the underside, screw goes in from top-down, and sits counterbored inside the printed part to avoid the sharp end of the bolt sticking in the air and causing this problem. SCAD and STL files linked below.

https://drive.google.com/drive/folders/1wAVW9g4GOHe4tTdY2j6lgEapmjQKBeSA?usp=sharing

mariusvw, 2019-05-20:
That is one part of the solution, will add the second solution to the cable holder later this evening.

Side-question, isn't it better to add the files in a pull request instead of Google Docs?

austinvojta, 2019-05-20:
Probably so! I have never made a full request before, don't know how to do
it. Also I think Prusa has reasoning to leave the screw entering from the
bottom - it leaves less chance to create a short circuit accidentally
between contacts on the bed if someone were inserting/removing screw while
bed is powered. So not sure they want to change the file.

On Mon, May 20, 2019, 2:33 AM Marius van Witzenburg <
notifications@github.com> wrote:

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

akukan, 2019-05-21:
We will go with similar solution as @austinvojta is suggesting, this is currently finishing tests and once goes to production it will be updated here - matter of days. It's already covered here atm https://manual.prusa3d.com/Guide/7.+Heatbed++&+PSU+assembly+(Black+PSU)/1153#s26163

mariusvw, 2019-05-21:
This solves the heatbed issue but are there also working plans on the Xaxis body/cable guide? Cause this is actually the reason why the wires get ~1.5mm lower than in the previous version.
Since the cable holder got removed from the repository I did not started on updating this part.

Another thing for the heatbed part is if you'd like I'd want to add in something to prevent short circuiting the heatbed wires.

gregsaun, 2019-05-21:
@akukan there is a risk that, during maintenance, someone shortcut + and - of the heated bed with the wrench. Maybe you can keep keep your previous solution and add a washer on the screw head.

Panayiotis-git, 2019-05-21:
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

gregsaun, 2019-05-21:
:satisfied: you know how that goes, we all went there I think... There is a safer way so why taking the risk?

mariusvw, 2019-05-22:
As part as a solution to this without reprinting the heatbed cover yet till feedback from Prusa I restored and adjusted the cable-holder.

There is an extra cable tie and angled cut-off close to the body to keep the wires up.

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

rrauenza, 2019-05-25:
@mariusvw Do you need help doing a pull request?

mariusvw, 2019-05-25:
@rrauenza no help needed, just didn't made one since my other PR's are not getting processed.

rrauenza, 2019-05-28:
> @rrauenza no help needed, just didn't made one since my other PR's are not getting processed.

For what it's worth, I did print yours out for my upcoming upgrade...  Thanks for the change.  You might also put it on thingiverse?

ManuGithubSteam, 2019-07-07:
Semms like a good improvement :-)

mariusvw, 2019-07-07:
> > @rrauenza no help needed, just didn't made one since my other PR's are not getting processed.
>
> For what it's worth, I did print yours out for my upcoming upgrade... Thanks for the change. You might also put it on thingiverse?

Uploaded here: https://www.thingiverse.com/thing:3733759

draeath, 2019-12-02:
I think this was fixed via e55953ff5189ca9b109a8d779e8a57ee6fd271e0 ?

draeath, 2019-12-02:
@akukan looks like you did in fact merge that change in, we can probably zap this issue!

e55953ff5189ca9b109a8d779e8a57ee6fd271e0

mariusvw, 2019-12-03:
@draeath, @akukan
Indeed look like it has been added... Just wondering, are you guys moving away from OpenSCAD?

Asking this because I see that the SCAD files are not matching with the current STL versions or the SCAD file is completely removed.

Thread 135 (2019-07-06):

MK3S: Unable to back off the filament on filament runout

maximlevitsky, 2019-07-06:
When filament runs out, it is often quite curled due to being on the inner diameter of the spool.
When the IR sensor detects the runout, user is asked to unload the filament but when this is attempted, the filament is stuck inside 'adapter-printer.stl' because it is a bit curled around the ball, and thus it doesn't hit the hole through which it was inserted in first place.

I manually fixed that by enlarging that hole, and adding a chamfer to the corresponding hole in the filament sensor cover from below.

ManuGithubSteam, 2019-07-07:
Hi
This seems like a good upgrade :-) Would you share your stls or design files ?
Thanks

maximlevitsky, 2019-07-07:
I did that in the old fashoned way, with a knife :)

tkircher, 2019-07-12:
I had this exact issue as well. Essentially every time I have a filament runout, I have to unscrew the idler and back the filament out with pliers. Don't really want to disassemble the hotend to fix it, since it happens so infrequently, but Prusa should really fix this.

PeterWelzien, 2020-04-06:
I also have this exact issue EVERY time I run out of filament. It's quite annoying having to open the idler and trying to get a hold of the filament with some pliers and pull them out. A fix would be much appreciated.

DWave42, 2020-04-14:
I am starting a chat with Prusa right now about this issue.

acetech09, 2020-04-18:
I've also had this issue every time I run out of filament, since I assembled the machine. I saw this thread a while ago, tried to chamfer/open up the holes, it still occurs.

tkircher, 2020-04-18:
The right solution is probably to move the head up and to the home position and then extrude out the rest of the filament, rather than trying to unload it.

bartlee01, 2020-08-17:
I have this same problem on Mk3S and Mk3S with MMU2S. I have been dealing with it by straightening or cutting off the kinked end of the filament but this program needs fixing. Another fix would be for the end bit of kinked filament to be much longer and have a rounded tip.

tkircher, 2020-08-17:
@akukan @josefprusa @veverkaondrej Still looking for a workaround on this issue. It's still an issue.

TurboCooler, 2021-01-04:
@akukan @josefprusa @veverkaondrej -- just lost a 20hr print because of this issue.   After the filament ran out, it was not able to retract the remaining filament.  I opened the door to remove the filament stuck in the extruder.  While doing so the X moved as the filament was really jammed.  The print did not recover and I lost the print.   A very SIMPLE solution would be to add code to firmware that when the filament runs out that the X/Y move to a corner and simply purges the remaining filament.  You have the signal that filament has runout.  You know the length that is left based on the height from the gear to the sensor.  Simply extrude that amount and allow someone to load additional filament and continue.   This would eliminate the problem completely.

bartlee01, 2021-01-04:
When filament runs out on mmu2s this problem is even worse. Unless you have manually straightened and cut a rounded point on the filament end it almost always gets stuck in the mmu2s on unload. It should park in a corner and give you the choice to either unload or purge the remaining filament.

tkircher, 2021-01-04:
@TurboCooler @bartlee01 Agreed that there should be an option to purge out the filament. Part of the problem is that the extruder gear can't drive the whole dead volume out of the extruder by itself, which is why I suspect they did it this way in the first place. But it's definitely superior to purge out the old filament with the new.

3d-gussner, 2021-01-05:
Hello everyone,
Nice to see some discussion here, but as this repository is related to the "**hardware**" design and not the firmware I think it is in the wrong place.
Please reopen a new issue [here](https://github.com/prusa3d/Prusa-Firmware/issues) if you think it is firmware related and close this issue here.

tkircher, 2021-01-06:
@3d-gussner This is still a hardware issue, but it may also be a firmware issue, or it's possible that the hardware can't be fixed and there can only be a workaround in firmware. TBD.

olilam, 2021-02-16:
Exact same issue on my last print! A fix would be great!

TheLion, 2021-03-28:
Just had the issue on 2 consecutive prints on my MK3S. I hadn't figured out the issue, but When reading te comments, I now know 😜.

I do wonder if the MK3S+ upgrade fixes this issue, as I already have the kit lying around 😉

Does anybody know if this is the case?

TurboCooler, 2021-03-28:
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

No, it does not.  The only thing that works provided you can catch it on time is to cut the end at 45 degrees so there is no hook or blob on filament on the end.  Then using your fingers make the end as straight as possible.  This works for me but it is a pain to time on very long prints.

The worst part of this problem is if you get a jam and while clearing it you move the head or plate even a tiny bit it will never be able to restart correctly.  If they homed the head or somehow reset where it left off it could work if you get a jam.  Glad to see I am not the only one with this issue and hopefully there is a fix.

tkircher, 2021-03-28:
Unfortunately, limit switches (or collision detection in the case of the Trinamic drivers) aren't precise enough for reliable re-homing. There just needs to be a better way to back out the filament and remove jams. Though, the MK3S+ did include some extruder tweaks to improve the situation.

UltraSalem, 2021-10-03:
It's been a while since I used it, but I seem to recall my mk2s runout sensor worked fine and the filament would back out and let me reload new filament without issue. Not sure what changed inside the extruder block for the mk3s to break it, but it jams backing out every time on my mk3s

napter, 2021-10-13:
Does anyone have a good solution to this other than snipping the filament end?  I was thinking of designing a mod to move the sensor up and out of the extruder body so that there is a gap where you can pull the filament out. I made a similar setup on my ender 5 but that sensor was separate to begin with.

lifewithmy3Dprinter, 2023-12-06:
I'm having the same issue. The filament gets stuck when trying to back out.

Three fixes:

- Ability to choose not to back it out, but rather purge it out while pushing new filament behind it.
- Add a chamfer or a wider hole for the filament to back out of.
- Do a homing routine after a new filament is ready to go. It's frustrating to loose a print because you accidentally move the extruder trying to get the stuck filament out.

ArmoredCarbon, 2024-07-07:
I am having this issue as well, and I always clip the bent ends of the filament and straighten it.
Has anyone come up with an easy solution yet?
If not I'm just going to rebuild the runout sensor which I know is going to be a complete pain.
My current idea is to drill it out and run a ptfe tube through the sensor assembly. A hole in the side of the tube should allow the sensor to detect the filament.

napter, 2024-07-15:
> I am having this issue as well, and I always clip the bent ends of the filament and straighten it. Has anyone come up with an easy solution yet? If not I'm just going to rebuild the runout sensor which I know is going to be a complete pain. My current idea is to drill it out and run a ptfe tube through the sensor assembly. A hole in the side of the tube should allow the sensor to detect the filament.

I made a very crude mod that takes the original sensor housing and puts it on a leg so it sits above the extruder. Since there is a gap between the sensor and the extruder, the bent end never goes into the extruder (and can be pulled out of the sensor if it didn't exit completely).

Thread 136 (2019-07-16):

PINDA holder sags in R4 revision

lff12, 2019-07-16:
After a lot of high temperature printing (Polymaker PC Max and generic HIPS), the PINDA holder begins to sag slightly, causing the sensor to tilt slightly to the left, and decreasing the accuracy of readings. Reseating the sensor and recalibrating the printer helps, but there is still a distinct sag. Parts for R4 self printed in Innofil PETG. Is it possible to reinforce the PINDA holder to prevent this?

prusa3d-bb, 2019-07-18:
Hello,
do you have any photos of this, which I could send to plastic parts developers? We are already reinforcing some parts, but I am not sure if this one is on the list too

Best Regards / S pozdravem
—
Jakub Kučera

Customer Support

_______________________________________

PRUSA Research

188/7a Partyzánská, 17000, Prague

+420 222 263 718

+421 220 570 305

Troubleshooting tutorials here!

Follow us on twitter and Facebook!

Check out our blog!

________________________________________

Please rate our reply ...be generous :-)

--- original message ---
On July 17, 2019, 1:42 AM GMT+2 notifications@github.com wrote:

After a lot of high temperature printing (Polymaker PC Max and generic HIPS), the PINDA holder begins to sag slightly, causing the sensor to tilt slightly to the left, and decreasing the accuracy of readings. Reseating the sensor and recalibrating the printer helps, but there is still a distinct sag. Parts for R4 self printed in Innofil PETG. Is it possible to reinforce the PINDA holder to prevent this?

—

You are receiving this because you are subscribed to this thread.

Reply to this email directly, view it on GitHub, or mute the thread.
--- end of original message ---

lff12, 2019-07-19:
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

lff12, 2019-07-19:
Sorry about the quality - i had a print in progress - but you can see that the PINDA is at an angle - its not caused by the position of the cable - it tilts to the right even if the cable is moved elsewhere.

prusa3d-bb, 2019-07-19:
Hello,
thank you for the photo. It is visible there. We are already reinforcing the parts around pinda probe. Do you need a replacement plastic part or can you print it yourself?

Best Regards / S pozdravem
—
Jakub Kučera

Customer Support

_______________________________________

PRUSA Research

188/7a Partyzánská, 17000, Prague

+420 222 263 718

+421 220 570 305

Troubleshooting tutorials here!

Follow us on twitter and Facebook!

Check out our blog!

________________________________________

Please rate our reply ...be generous :-)

--- original message ---
On July 19, 2019, 2:27 AM GMT+2 notifications@github.com wrote:

Sorry about the quality - i had a print in progress - but you can see that the PINDA is at an angle - its not caused by the position of the cable - it tilts to the right even if the cable is moved elsewhere.

—

You are receiving this because you commented.

Reply to this email directly, view it on GitHub, or mute the thread.
--- end of original message ---

lff12, 2019-07-21:
Very happy to print it myself, thanks! It also seems to be touching the cover and melting there - seems there is less gap between the heatsink and bottom of the cover than previous version! Thanks though.

lff12, 2019-07-27:
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
Here is a few photos of the old body after removal. Interestingly the fan part is perfect, it's just the body and cover that deformed. I'm replacing the parts today so will report back

lff12, 2019-07-27:
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

prusa3d-bb, 2019-07-29:
Hello,
thank you for the photos. The reinforced parts are done. You can print them. https://github.com/prusa3d/Original-Prusa-i3/tree/MK3S/Printed-Parts/STL

Best Regards / S pozdravem
—
Jakub Kučera

Customer Support

_______________________________________

PRUSA Research

188/7a Partyzánská, 17000, Prague

+420 222 263 718

+421 220 570 305

Troubleshooting tutorials here!

Follow us on twitter and Facebook!

Check out our blog!

________________________________________

Please rate our reply ...be generous :-)

--- original message ---
On July 27, 2019, 6:46 PM GMT+2 notifications@github.com wrote:

—

You are receiving this because you commented.

Reply to this email directly, view it on GitHub, or mute the thread.
--- end of original message ---

maximlevitsky, 2019-07-29:
Thank you!
Note that in my case the extruder cover melted right away after I preheated the printer to just PETG temperatures.
PINDA seems to hold up, though.

lff12, 2019-07-29:
I've printed it, twice. First one had a small crack around the PINDA holder - but around the area where the screw and nut is so still holds ok - printed a second one. Have run a few prints with temps up to 270C - so far so good - will see in about 6 weeks if its still staying straight.

prusa3d-bb, 2019-07-30:
Hello,
if anything happens. please let us know, so we could reinforce it even more. Thank you

Best Regards / S pozdravem
—
Jakub Kučera

Customer Support

_______________________________________

PRUSA Research

188/7a Partyzánská, 17000, Prague

+420 222 263 718

+421 220 570 305

Troubleshooting tutorials here!

Follow us on twitter and Facebook!

Check out our blog!

________________________________________

Please rate our reply ...be generous :-)

--- original message ---
On July 30, 2019, 1:11 AM GMT+2 notifications@github.com wrote:

I've printed it, twice. First one had a small crack around the PINDA holder - but around the area where the screw and nut is so still holds ok - printed a second one. Have run a few prints with temps up to 270C - so far so good - will see in about 6 weeks if its still staying straight.

—

You are receiving this because you commented.

Reply to this email directly, view it on GitHub, or mute the thread.
--- end of original message ---

prusa3d-bb, 2019-07-31:
Hello,
could you please send me a photo of the new reinforced hotend cover, which was melted already? So it really melted after first heat up?

Best Regards / S pozdravem
—
Jakub Kučera

Customer Support

_______________________________________

PRUSA Research

188/7a Partyzánská, 17000, Prague

+420 222 263 718

+421 220 570 305

Troubleshooting tutorials here!

Follow us on twitter and Facebook!

Check out our blog!

________________________________________

Please rate our reply ...be generous :-)

--- original message ---
On July 30, 2019, 5:44 PM GMT+2 info@prusa3d.com wrote:

Hello,

if anything happens. please let us know, so we could reinforce it even more. Thank you

Best Regards / S pozdravem

—

Jakub Kučera

Customer Support

_______________________________________

PRUSA Research

188/7a Partyzánská, 17000, Prague

+420 222 263 718

+421 220 570 305

Troubleshooting tutorials here!

Follow us on twitter and Facebook!

Check out our blog!

________________________________________

Please rate our reply ...be generous :-)

> On July 30, 2019, 1:11 AM GMT+2 notifications@github.com wrote:

> I've printed it, twice. First one had a small crack around the PINDA holder - but around the area where the screw and nut is so still holds ok - printed a second one. Have run a few prints with temps up to 270C - so far so good - will see in about 6 weeks if its still staying straight.

> —

> You are receiving this because you commented.

> Reply to this email directly, view it on GitHub, or mute the thread.
--- end of original message ---
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
maximlevitsky, 2019-07-31:
Also it probably helped that ambients are here around 30C. (I basically have two choices: suffer from AC noise, or suffer from heat... )

Moorviper, 2019-09-11:
Why not use just ABS for the extruder part.
Many PETG are not better than PLA and deform when warmed up to 55-60°C for a longer period.

francisdb, 2019-09-15:
Same problem here since I built the [prusa lack enclosure](https://blog.prusaprinters.org/cheap-simple-3d-printer-enclosure/). I print a lot of PC / Nylon at high temperatures and the ambient temp in the enclosure reaches 35-40°C. The pinda probe started sagging and had to re-calibrate 1st layer twice already.

For reference:
https://forum.prusaprinters.org/forum/original-prusa-i3-mk3s-mk3-hardware-firmware-and-software-help/mk3s-part-melted/

Has the pinda probe part also been reinforced or only the cover? Any suggestions for a better material than PETG for this part?

prusa3d-bb, 2019-09-18:
Hello,
pinda probe holder has been also reinforced as you can see here https://github.com/prusa3d/Original-Prusa-i3/tree/MK3S/Printed-Parts/STL
I recommend using PETG or ABS/ASA. We just released Prusament ASA, which you can use.

Best Regards / S pozdravem
—
Jakub Kučera

Customer Support

_______________________________________

PRUSA Research

188/7a Partyzánská, 17000, Prague

+420 222 263 718

+421 220 570 305

Troubleshooting tutorials here!

Follow us on twitter and Facebook!

Check out our blog!

________________________________________

Please rate our reply ...be generous :-)

--- original message ---
On September 15, 2019, 9:25 AM GMT+2 notifications@github.com wrote:

Same problem here since I built the prusa lack enclosure. I print a lot of PC / Nylon at high temperatures and the ambient temp in the enclosure reaches 35-40°C. The pinda probe started sagging and had to re-calibrate 1st layer twice already.

For reference:

https://forum.prusaprinters.org/forum/original-prusa-i3-mk3s-mk3-hardware-firmware-and-software-help/mk3s-part-melted/

Has the pinda probe part also been reinforced or only the cover? Any suggestions for a better material than PETG for this part?

—

You are receiving this because you were mentioned.

Reply to this email directly, view it on GitHub, or mute the thread.
--- end of original message ---

embusalacchi, 2019-10-07:
Hi!  Just wanted to report that my original hot end cover has started to sag with only PETG printing.  I was printing the replacement in PETG so I'm glad that's when it started to sag.  I'm not seeing it with the PINDA holder though.  I plan on replacing the cover in the next few days assuming I get the time.  I can report back if it sags again.

Rubines, 2020-02-03:
Hi

I also had thes sagging pinda problem and ignored it, until the probe holder broke,..
The problematic section is where the square nut is positionend, there is verry little supporting structure around it. Unfortunately I cannot find the improved version anymore, the R4 Version started to sag pretty quickly.
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

prusa3d-bb, 2020-02-04:
Hello,
please contact Prusa support directly on the email info@prusa3d.com or on the online chat, which is located on the eshop bottom right corner to sort out the replacement of this part. Thank you

wjsteele, 2020-04-07:
Just as an FYI... I just experienced this same failure during an extended print at 250C (Prusament PETG) where the Pinda probe sagged and came in contact with the print.  I was able to pause the print and move it up, but will need to repair it before the next print.

rafepurnell, 2020-04-26:
I have had the same issue and have melted 3 of these reinforced PINDA holders. I'm starting to worry about finding a solution.

Right now my CR10 is my savoir.

Is the right path to get the BondTech upgrade or is there another solution for this problem.

I loved my MK3 before the MK3S upgrade. :(

observatoer, 2020-04-26:
Based on what I have tried, the Bondtech upgrade extruder and the Bear extruder have both no issue with the pinda holder. You shall to run them with a Sunon fan to cool the hotted properly.

Rubines, 2020-04-28:
Hi

The new design update solved all my troubles even when printing @250 °C for 18 hours.
At first I was sceptic but after a while all my concerns were gone.

Prusa-Support, 2022-05-10:
Hello! Sorry for the late response to this thread. Closing the thread as the reinforcing aspect is solved - of course, in case of any further specific issues related with this, do not hesitate to let us know by contacting our Technical Support info@prusa3d.com at any time, we'll help with anything and check each case one by one.

Alessandro Pantaleo
Prusa Research

Closed 2022-05-10.

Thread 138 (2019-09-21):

MK3S - Random print fail partway through

tmfksoft, 2019-09-21:
I've just received my MK3S aand assembled it.

But partway through a print, at random it suddenly raises the Z axis, the print bed goes all the way to the back and repeatedly goes forward a few times then the X axis flies off to the right and jams.
After is done what I can only refer to as a stroke it goes back to printing but the X axis is now offset by half the print bed size and tries to print on the side of the print bed.

Here's a badly recorded clip:
https://files.minio.thomas-edwards.me/2019/09/21/2019-09-21_23-56-08.webm

Here's the GCode:
https://files.minio.thomas-edwards.me/2019/09/21/2019-09-21_23-57-47.gcode

Generated using Cura 4.2.1 using the Prusa Printer and Profiles.

You can see it printing normally and properly.
Then randomly it'll do its stroke thing then repeatedly raising up.
This happens at random. I've tried the same print twice with it doing it both times at different points within the print.

I can only assume its a firmware thing due to it doing it at random. I've had a few successful prints without this happening but I can't take my eyes off the printer incase it does it.

Panayiotis-git, 2019-09-22:
It looks like your X axis is very tight or the extruder cannot move smoothly. If I understand it correctly, the printer detects a crash. It tries to re-home and it fails to move the X-axis to the very left position.

Are you sure that your X-axis has been assembled properly? Try to remove the belt and move the extruder from the left edge to the rightmost edge and back. You should not feel any resistance. If you feel like you have to push the extruder to move it, then try to un-tight a little the back carriage screws.

tmfksoft, 2019-09-22:
After some bothering others on Twitter I got the same suggestion.
I loosened the belt until the belt status read 265 instead of 255.

After that I had much more success, however it's failed once again 9hrs into a 9hr 42min print which is gutting. The print has come out absolutely perfect up until it failed.

I'm really not sure what's causing this currently. I'll have to try disabling crash detection and see how the prints go afterwards.

tmfksoft, 2019-10-06:
Forgot to update this issue.

After tightening the X belt until it was within the recommended range I was able to print for longer until crash detection kicked in once again.

I disabled crash detection and have made many prints since then, all prints have turned out perfectly fine.

I dont understand what constitutes as a crash for the crash detection to kick in but I've printed many hours of prints since disabling it without issue.

I can only assume the crash detection is over sensitive?

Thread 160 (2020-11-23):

[Question] Why do some nozzles types have such low torque setting as 1.5Nm?

mop999x, 2020-11-23:
i have a mk3s and having some nozzle issues so i did some research due to nozzle leaks and was wondering why prusa/e3d suggest to use 2.5-3Nm (i believed this to be universal for all nozzle types regardless of manufacture) torque on nozzle to tighten it but other sources i found mostly for other nozzle types (Tungsten carbide) suggest torque of no more then 1.5NM, here are few examples

https://docs.dyzedesign.com/nozzles.html#install-your-tungsten-carbide-nozzle

and i believe even 3d maker engendering says the same

do you know why that is?

i just wanted to know why tightening nozzle at 3NM that say 1.5Nm would cause a leak, if it would ?

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

tomavisar, 2020-12-07:
What does this have to do with this? Also it's because different materials have different levels of thermal expansion

Prusa-Support, 2022-05-10:
Hello!
I am sorry for the late response to this thread. We can think of the nozzle as any bolt, so depending on the bolt at hand the manufacturer specifies a maximum torque to be applied. If we apply too much torque, we'd have a risk of damaging, deforming, stripping the bolt, which can result in a loose joint. Leaking filament from above the heater block is a result of a loose joint between nozzle and heatbreak.

So in this case, the too much torque could have caused deformation, stripping, which might have led to a poor joint nozzle-heatbreak which causes the leaking. I'd recommend checking if also using the correct torque spec would not solve the issue - in that case, the loose joint would be likely caused, provided that nozzle and heatbreak are compatible, by a badly positioned heatbreak (can be inadvertently raised during the nozzle change procedure).

Alessandro Pantaleo
Prusa Research

Closed 2022-05-10.

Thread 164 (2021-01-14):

Extruder body part breaks repeatedly

tkapler, 2021-01-14:
I tried to print twice https://github.com/prusa3d/Original-Prusa-i3/blob/MK3S/Printed-Parts/STL/extruder-body.stl part and both times it broke on similar place (even once i printed it with other parts on the bed and second time separately). All the other parts were OK. I have used ABS instead of PETG, so that may be part of the reason but still i think there s probably some problem on this place and probably some reinforcement would help.
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

tkapler, 2021-01-15:
small update - tried for the 3rd time, same settings as the second, just used corex - the same problem in exact same spot as the image on the left. I am looking to the slicer, it seems it always happens at the layer 152 (16.2mm), where bridge infill changes the way it prints. I am now trying to add support enforcers around the area, so that there would't be so big stress.

stahlfabrik, 2021-01-15:
The layer adhesion seems to be lacking. Are you cooling the abs print? You should tune your settings for optimal layer strength.

I failed printing the parts (years ago) in abs-t. When they were nice and accurate, layer adhesion was lacking. With no cooling they were strong but inaccurate in shape.

So I printed in petg as recommended and did not look back

tkapler, 2021-01-15:
All other prints were without any problem, they are perfect (the photo exaggerates some asspects, but in real life they are really smoothe and nice. I have used both default Prusa settings and that presented in the 3MF
just the info of the 4th print - adding supports helped.

Panayiotis-git, 2021-01-15:
Perhaps increasing the perimeters at this area would help.

shawntexan, 2021-02-24:
do 100% infill to ensure strength and lasting there is a lot of heat to deal with. all my parts i print 100%

Moorviper, 2021-02-25:
more perimeters is more efficient than 100% infill...

steakknife, 2021-11-15:
Printed in black Prusa PETG included with the M3KS+ upgrade kit. The bed sensor holder outside failed to print correctly exactly as in the first picture on the LEFT side. 20% infill as recommended and added 5 mm brim. Printed on PEI-laminated flat steel sheet with adequate Layerneer Bed Weld. Retrying with 100% infill.

dougshell, 2022-08-21:
The same part failed in the same way on my end printing in ASA on a Ultistik textured bed (that apparently has such good adhesion I need to use glue according to PRUSA). I have no other adhesion issues with my printer and have been printing on it for almost 2 years.  The same part failed in the same way on a Voron that was for a PIF order for ASA Prusa parts.

Prusa-Support, 2022-09-02:
Thank you for reaching us.

This part was designed with PETG material in mind and tested with it. Materials like ABS/ASA have substantially different characteristics. PETG offers good dimensional accuracy while ABS/ASA are well-known for their infamous tendency to shrink and consequent poor first layer adhesion.

For instance, the prints of the main post may have failed because of a poor first-layer contact area of the detached PINDA mount piece [left] or poor layer-to-layer adhesion and dimensional stability [right]. This is based on a quick guess but the reason for the print failure could be a more complex mixture of factors.
- In the first case, you may want to review the first layer quality and the spring sheet [preparation according to the material](https://help.prusa3d.com/category/material-guide_220), or maybe add a [helper disk](https://help.prusa3d.com/article/shape-gallery_301453) at the bottom.
- In the second case, you may want to improve layer adhesion (rise the temperature, reduce the speed...), and in the case of ABS/ASA avoid thermal shocks as much as possible (warm ambient, weak or disabled print fan cooling...). Also, please notice the PINDA mount connection has sharp angles which probably won't help in case of strong shrinkage materials.

Our factory printed parts used to be printed in ABS a few years ago. We have reason to believe that PETG is more suitable for structural parts, and we switched to PETG as soon as the textured sheet prototypes came out.

I don't really see a concern about the part design so, if all your questions are answered, I suggest closing this issue and getting in touch with our Customer Support for troubleshooting.
https://help.prusa3d.com/article/customer-support_2287

Michele Moramarco
Prusa Research

Prusa-Support, 2022-09-22:
I believe this issue can be closed now.

This may seem to be a problem of printing, that could be solved through a proper troubleshooting session, and it is not necessarily related to the printer design.
Please consider reaching our Customer Support for help with similar issues.

Thanks for understanding.

Michele Moramarco
Prusa Research

Closed 2022-09-22.

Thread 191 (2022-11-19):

Prusa MK3S+ Z smooth rod is not flush with Z axis top parts

SuperNeko, 2022-11-19:
Hello!
I have a question about Z axis smooth rod and Z top plastic part. I assembled my printer (Original Prusa i3 MK3S+) sometime ago, but only now I noticed that I am able to move Z smooth rod up and down relatively freely, because Z smooth rod is not flush with Z axis top parts.
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
Although it does not move in XY directions, it can be moved in Z axis directions.
I am sure that smooth rods are fully seated in both Z axis motor mounts.
I also inspected official 3D viewer model and it has the same thing.
https://drive.autodesk.com/de296501e/shares/SH9285eQTcf875d3c539d9640fa5f8e3afd8
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
I do not have any problems yet (and by googling this "problem", looks like no one has), **but I am generously interested, if there is any explanation why it is designed like this?** While it it does not impact use of printer, all other axis smooth rods are constrained in all axes.
Like X and Y smooth rod do not move in any direction.

For example, in Prusa Bear mod, Z axis smooth rod are flush with the Z axis top parts.
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

Prusa-Support, 2022-12-09:
Hello! The reason for it is to allow for very slight tolerances in the length of Z-axis smooth rods. 🙂

Alessandro Pantaleo
Prusa Research

mikromCZ, 2022-12-09:
Just put a M3 nut on the top of the rod before you mount the top part 😎

Closed 2022-12-09.

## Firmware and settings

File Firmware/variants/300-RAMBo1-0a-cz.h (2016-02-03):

#ifndef CONFIGURATION_PRUSA_H
#define CONFIGURATION_PRUSA_H

/*------------------------------------
    GENERAL SETTINGS
*------------------------------------*/

// Printer revision
#define REVISION "300-1a"
#define THREEMM_PRINTER   

// Printer name
#define CUSTOM_MENDEL_NAME "Prusa i3"

// Electronics
#define MOTHERBOARD BOARD_RAMBO_MINI_1_0

// Language setting
#define LANGUAGE_INCLUDE GENERATE_LANGUAGE_INCLUDE(cz)


/*------------------------------------
    AXIS SETTINGS
*------------------------------------*/

// Steps per unit {X,Y,Z,E}
#define DEFAULT_AXIS_STEPS_PER_UNIT   {100,100,3200/0.8,350*1.5} 

// Endstop inverting
const bool X_MIN_ENDSTOP_INVERTING = false; // set to true to invert the logic of the endstop.
const bool Y_MIN_ENDSTOP_INVERTING = false; // set to true to invert the logic of the endstop.
const bool Z_MIN_ENDSTOP_INVERTING = false; // set to true to invert the logic of the endstop.

// Home position
#define MANUAL_X_HOME_POS 0
#define MANUAL_Y_HOME_POS 0
#define MANUAL_Z_HOME_POS 0.25

// Travel limits after homing
#define X_MAX_POS 214
#define X_MIN_POS 0
#define Y_MAX_POS 198
#define Y_MIN_POS 0
#define Z_MAX_POS 201
#define Z_MIN_POS 0.23

#define NUM_AXIS 4 // The axis order in all axis related arrays is X, Y, Z, E
#define HOMING_FEEDRATE {3000, 3000, 240, 0}  // set the homing speeds (mm/min)

#define DEFAULT_MAX_FEEDRATE          {500, 500, 3, 25}    // (mm/sec)
#define DEFAULT_MAX_ACCELERATION      {9000,9000,30,10000}    // X, Y, Z, E maximum start speed for accelerated moves. E default values are good for Skeinforge 40+, for older versions raise them a lot.

#define DEFAULT_ACCELERATION          3000    // X, Y, Z and E max acceleration in mm/s^2 for printing moves
#define DEFAULT_RETRACT_ACCELERATION  3000   // X, Y, Z and E max acceleration in mm/s^2 for retracts


#define MANUAL_FEEDRATE {3000, 3000, 240, 60}   // set the speeds for manual moves (mm/min)


/*------------------------------------
    EXTRUDER SETTINGS
*------------------------------------*/

// Mintemps
#define HEATER_0_MINTEMP 15
#define HEATER_1_MINTEMP 5
#define HEATER_2_MINTEMP 5
#define BED_MINTEMP 15

// Maxtemps
#define HEATER_0_MAXTEMP 315
#define HEATER_1_MAXTEMP 275
#define HEATER_2_MAXTEMP 275
#define BED_MAXTEMP 150

// Define PID constants for extruder
#define  DEFAULT_Kp 12.7
#define  DEFAULT_Ki 1.09
#define  DEFAULT_Kd 37.4

// Extrude mintemp
#define EXTRUDE_MINTEMP 190

// Extruder cooling fans
#define EXTRUDER_0_AUTO_FAN_PIN   6
#define EXTRUDER_1_AUTO_FAN_PIN   -1
#define EXTRUDER_2_AUTO_FAN_PIN   -1
#define EXTRUDER_AUTO_FAN_TEMPERATURE 50
#define EXTRUDER_AUTO_FAN_SPEED   255  // == full speed



/*------------------------------------
    LOAD/UNLOAD FILAMENT SETTINGS
*------------------------------------*/

// Load filament commands
#define LOAD_FILAMENT_0 "M83"
#define LOAD_FILAMENT_1 "G1 E65 F400"
#define LOAD_FILAMENT_2 "G1 E40 F100"

// Unload filament commands
#define UNLOAD_FILAMENT_0 "M83"
#define UNLOAD_FILAMENT_1 "G1 E-80 F400"

/*------------------------------------
    CHANGE FILAMENT SETTINGS
*------------------------------------*/    

// Filament change configuration
#define FILAMENTCHANGEENABLE
  #ifdef FILAMENTCHANGEENABLE
    #define FILAMENTCHANGE_XPOS 211
    #define FILAMENTCHANGE_YPOS 0
    #define FILAMENTCHANGE_ZADD 2
    #define FILAMENTCHANGE_FIRSTRETRACT -2
    #define FILAMENTCHANGE_FINALRETRACT -80
    
    #define FILAMENTCHANGE_FIRSTFEED 70
    #define FILAMENTCHANGE_FINALFEED 50
    #define FILAMENTCHANGE_RECFEED 5

    #define FILAMENTCHANGE_XYFEED 70
    #define FILAMENTCHANGE_EFEED 20
    #define FILAMENTCHANGE_RFEED 400
    #define FILAMENTCHANGE_EXFEED 2
    #define FILAMENTCHANGE_ZFEED 300
    
#endif

/*------------------------------------
    ADDITIONAL FEATURES SETTINGS
*------------------------------------*/  

// Define Prusa filament runout sensor
//#define FILAMENT_RUNOUT_SUPPORT

#ifdef FILAMENT_RUNOUT_SUPPORT
    #define FILAMENT_RUNOUT_SENSOR 1
#endif

/*------------------------------------
    MOTOR CURRENT SETTINGS
*------------------------------------*/  

// Motor Current setting for BIG RAMBo
#define DIGIPOT_MOTOR_CURRENT {135,135,135,135,135} // Values 0-255 (RAMBO 135 = ~0.75A, 185 = ~1A)
#define DIGIPOT_MOTOR_CURRENT_LOUD {135,135,135,135,135}

// Motor Current settings for RAMBo mini PWM value = MotorCurrentSetting * 255 / range
#if MOTHERBOARD == 102 || MOTHERBOARD == 302
  #define MOTOR_CURRENT_PWM_RANGE 2000
  #define DEFAULT_PWM_MOTOR_CURRENT  {270, 450, 850} // {XY,Z,E}
  #define DEFAULT_PWM_MOTOR_CURRENT_LOUD  {540, 450, 500} // {XY,Z,E}
#endif

/*------------------------------------
    PREHEAT SETTINGS
*------------------------------------*/  

#define PLA_PREHEAT_HOTEND_TEMP 220
#define PLA_PREHEAT_HPB_TEMP 50
#define PLA_PREHEAT_FAN_SPEED 255

#define ABS_PREHEAT_HOTEND_TEMP 285
#define ABS_PREHEAT_HPB_TEMP 100
#define ABS_PREHEAT_FAN_SPEED 255

#define HIPS_PREHEAT_HOTEND_TEMP 220
#define HIPS_PREHEAT_HPB_TEMP 100
#define HIPS_PREHEAT_FAN_SPEED 0 

#define PP_PREHEAT_HOTEND_TEMP 254
#define PP_PREHEAT_HPB_TEMP 100
#define PP_PREHEAT_FAN_SPEED 0 

#define PET_PREHEAT_HOTEND_TEMP 240
#define PET_PREHEAT_HPB_TEMP 90
#define PET_PREHEAT_FAN_SPEED 0 

#define FLEX_PREHEAT_HOTEND_TEMP 250
#define FLEX_PREHEAT_HPB_TEMP 50
#define FLEX_PREHEAT_FAN_SPEED 0 


/*------------------------------------
    THERMISTORS SETTINGS
*------------------------------------*/

//
//--NORMAL IS 4.7kohm PULLUP!-- 1kohm pullup can be used on hotend sensor, using correct resistor and table
//
//// Temperature sensor settings:
// -2 is thermocouple with MAX6675 (only for sensor 0)
// -1 is thermocouple with AD595
// 0 is not used
// 1 is 100k thermistor - best choice for EPCOS 100k (4.7k pullup)
// 2 is 200k thermistor - ATC Semitec 204GT-2 (4.7k pullup)
// 3 is Mendel-parts thermistor (4.7k pullup)
// 4 is 10k thermistor !! do not use it for a hotend. It gives bad resolution at high temp. !!
// 5 is 100K thermistor - ATC Semitec 104GT-2 (Used in ParCan & J-Head) (4.7k pullup)
// 6 is 100k EPCOS - Not as accurate as table 1 (created using a fluke thermocouple) (4.7k pullup)
// 7 is 100k Honeywell thermistor 135-104LAG-J01 (4.7k pullup)
// 71 is 100k Honeywell thermistor 135-104LAF-J01 (4.7k pullup)
// 8 is 100k 0603 SMD Vishay NTCS0603E3104FXT (4.7k pullup)
// 9 is 100k GE Sensing AL03006-58.2K-97-G1 (4.7k pullup)
// 10 is 100k RS thermistor 198-961 (4.7k pullup)
// 11 is 100k beta 3950 1% thermistor (4.7k pullup)
// 12 is 100k 0603 SMD Vishay NTCS0603E3104FXT (4.7k pullup) (calibrated for Makibox hot bed)
// 13 is 100k Hisens 3950  1% up to 300°C for hotend "Simple ONE " & "Hotend "All In ONE" 
// 20 is the PT100 circuit found in the Ultimainboard V2.x
// 60 is 100k Maker's Tool Works Kapton Bed Thermistor beta=3950
//
//    1k ohm pullup tables - This is not normal, you would have to have changed out your 4.7k for 1k
//                          (but gives greater accuracy and more stable PID)
// 51 is 100k thermistor - EPCOS (1k pullup)
// 52 is 200k thermistor - ATC Semitec 204GT-2 (1k pullup)
// 55 is 100k thermistor - ATC Semitec 104GT-2 (Used in ParCan & J-Head) (1k pullup)
//
// 1047 is Pt1000 with 4k7 pullup
// 1010 is Pt1000 with 1k pullup (non standard)
// 147 is Pt100 with 4k7 pullup
// 110 is Pt100 with 1k pullup (non standard)

#define TEMP_SENSOR_0 1
#define TEMP_SENSOR_1 0
#define TEMP_SENSOR_2 0
#define TEMP_SENSOR_BED 1


#endif //__CONFIGURATION_PRUSA_H

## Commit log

2015-12-23 Firmware parametrization, scrolling long text on LCD and cleanup
    [Configuration.h, Configuration_adv.h]
2016-01-26 Fixed beeping, knob sensitivity decreased, only one character displayed after scrolling fixed, M27 command returning filename and time elapsed, fixed XY and E PWM channels mismatch
    [Configuration.h, Configuration_adv.h]
2016-02-03 Added printed parts, firmware motor current switching, added live Z adjusting, more parametrized and minor cleanup
    [5015housing-MK3.dxf, 5015housing-MK3.scad, 5015housing-MK3.stl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]
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2016-02-18 Fixed temperature range when setting from LCD
2016-02-19 Version 2.2.3 live Language setting, Language reset when holding knob during startup, revision names redesigned, minor tweeks and cleanup
    [Configuration.h]
2016-02-20 Removed firmware files -> moved to another repo
    [Configuration.h, Configuration_adv.h]
2016-03-10 Extruder part fixed
    Fixed corrupted extruder model
    [extruder-carriage-side.stl, extruder-motor-side.stl, main.scad]
2016-03-13 X-ends for leadscrew
    Modified X-ends for Tr8x8 nut
    [x-end-idler.stl, x-end-motor.stl, x-end.scad]
2016-03-16 Moved hole for belt guide
    Moved hole for belt guide to make 250mm X movement possible.
    [x-end-idler.scad, x-end-idler.stl]
2016-03-16 X-end-motor modified
    X-end-motor is now holding the X endstop
    [x-end-motor.scad]
2016-03-16 Modified dimensions and new belt trap system
    Modified dimension of whole carriage to allow full 250mm travel
    distance and new belt trap for easier assembly
    [x-carriage.scad]
2016-03-16 Changed pitch of Z rods and motors
    [z-axis-bottom.scad, z-axis-top.scad]
2016-03-16 Modified for 210mm travel distance
    [y-corners.scad]
2016-04-16 New extruder design
    Extruder design and naming changed
    [extruder-body.scad, extruder-body.stl, extruder-carriage-side.scad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]
2016-04-16 Minor tweaks
    Extruder parts as modules and generated new STL for x-carriage
    [extruder-body.scad, extruder-cover.scad, extruder-cover.stl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]
2016-04-16 Cable trays
    Added cable trays for better cable management.
    [x-carriage.scad, x-carriage.stl]
2016-04-16 Cable guide for P.I.N.D.A. probe and print fan
    Added cable hook to the extruder to guide cables to the tray in carriage
    [extruder-body.stl, extruder-main.scad]
2016-04-16 P.I.N.D.A. probe mounting improved
    More rigid and easier to adjust
    [extruder-body.stl, extruder-main.scad]
2016-04-17 Fan nozzle
    Fan nozzle designed, new stl of extruder body and modified air path on
    extruder cover + mount for nozzle
    [extruder-body.stl, extruder-cover.stl, extruder-main.scad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]
2016-04-18 Fan nozzle update and Cable management
    [bearing.scad, extruder-main.scad, fan-nozzle.scad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]
2016-04-19 Cable management
    Improved cable management
    [x-carriage.scad, x-carriage.stl]
2016-04-24 Removed old files, improved print cooling
    [5015housing-MK3.dxf, 5015housing-MK3.scad, LCD_Cover.STL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]
2016-04-24 Z screw cover added
    Z screw cover preventing feeding the mess into the motor
    [z-screw-cover.scad, z-screw-cover.stl]
2016-04-24 New Y belt holder
    New design of Y belt holder for easier assembly
    [y-belt-holder.scad, y-belt-holder.stl]
2016-04-24 Stability reinforcement
    Modified PSU cover and added new part for better frame stability
    [PSU-Y-part.scad, PSU-Y-part.stl, PSU-cover-NODRILL.scad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]
2016-04-24 X-ends tweaked
    Smoothed holes, pitch adjusting screws and minor tweaks for easier
    assembly
    [x-end-idler.scad, x-end-idler.stl, x-end-motor.scad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]
2016-04-24 New idler
    New extruder idler for current extruder design
    [extruder-idler.scad, extruder-idler.stl]
2016-04-24 X carriage improvement
    New cable management system
    [x-carriage.scad, x-carriage.stl]
2016-04-24 Y axis redesign
    Y endstop moved on Y-motor mount, Y axis moved up and holes for bearing
    expanded
    [bearing.scad, y-corners.scad, y-corners.stl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]
2016-04-24 Z axis improvement
    Improved Z axis parts to prevent Z lead screw from bending
    [z-axis-bottom.scad, z-axis-bottom.stl, z-axis-top.scad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]
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2016-05-02 Better P.I.N.D.A. probe mount and extruder cable path
    [extruder-body.stl, extruder-main.scad, x-carriage.scad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]
2016-05-05 Modified Idler
    Extruder idler modified for easier printing
    [extruder-idler.scad, extruder-idler.stl]
2016-05-05 Heatbed cable cover
    Printed part covering cables from heatbed
    [heatbed_cable_cover.scad, heatbed_cable_cover.stl]
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2016-05-05 STL regenerated, centered and Fixed spool holder
    STL files are generated again, properly rotated and centered.
    Spool holder is now generating both parts at once .
    [LCD-SupportA.stl, LCD-SupportB.stl, PSU-Y-part.stl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]
2016-05-05 LCD cable clips
    Clips for safer anchoring of cables from LCD
    [LCD-cable-clip.scad, LCD-cable-clip.stl]
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2016-05-10 PSU Cover fixed
    Bad polygon causing slicer issues fixed
    [PSU-cover-NODRILL.scad, PSU-cover-NODRILL.stl]
2016-05-10 Y-corner easier assembly
    Smooth rod gap filled for easier assembly
    [y-corners.scad, y-corners.stl]
2016-05-12 Extruder clearance tweaked
    Tweaked tolerances for better assembly and square nuts.
    [extruder-body.stl, extruder-main.scad]
2016-05-12 Y motor holder updated
    Modified endstop holder on Y-motor for easier assembly
    [y-motor.scad, y-motor.stl]
2016-05-12 x-end idler modified
    Modified nut traps for square nuts
    [x-end-idler.scad, x-end-idler.stl]
2016-05-12 X-ends modified
    Modified waste pocket for easier assembly
    [x-end-idler.scad, x-end-idler.stl, x-end-motor.scad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]
2016-05-13 LCD cover reset knob cut
    Reset knob nipple is now shorter for safer operation
2016-05-13 PSU cover update
    M3 reinforcement screws slots
    [PSU-cover-NODRILL.scad, PSU-cover-NODRILL.stl]
2016-05-15 Y-belt-holder fixed
    Fixed belt holder (wrong version with improper endstop mount)
    [y-motor.scad, y-motor.stl]
2016-05-28 New Y-corners
    Deeper LM8UU keepout and moved ziptie for safer operation of Y axis
    [y-corners.scad, y-corners.stl]
2016-05-28 Y-belt holder modified
    Tighter gap for belt
    [y-belt-holder.scad, y-belt-holder.stl]
2016-05-28 X-carriage updated
    Bigger bearing holes for easier assembly and fixed 2D manifold issues
    [bearing.scad, x-carriage.scad, x-carriage.stl]
2016-05-28 PSU-cover update
    Reinforcement screw slots rotated
    [PSU-cover-NODRILL.scad, PSU-cover-NODRILL.stl]
2016-05-28 X-ends update
    Endstop key added and slightly expanded bearing and nuts holes
    [x-end-idler.stl, x-end-motor.scad, x-end-motor.stl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]
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2016-10-25 Y-distance added
    Part to keep Y axis motor aligned with rods
    [Y-distance.scad]
2017-01-31 Add files via upload
    Fixed incorrect export to stl resulting in "facet normal nan nan nan"
    [x-carriage.scad]
2017-01-31 Fixed incorrect export to stl resulting in "facet normal nan nan nan"
    [x-carriage.stl]
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2018-02-11 removed, replaced by y-rod-holder
    [y-holder-front.scad]
2018-02-11 screws and nuts tolerances
    [extruder-idler.scad, y-belt-holder.scad, y-belt-idler.scad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]
2018-02-11 screws & nuts tolerances , rotated to proper print position
    [extruder-body.scad]
2018-02-11 extruder screw clearance, tolerances
    [extruder-cover.scad]
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2018-02-11 motor opening, tolerances
    [y-motor-holder.scad]
2018-02-11 thin wall cut, tolerances
    [x-carriage-back.scad]
2018-02-11 belt tensioner, pulley screw fix, trapeziod nut reinforcement, tolerances
    [x-end-idler.scad, x-end-motor.scad, x-end.scad]
2018-02-11 Belt holder change, tolerances
    [x-carriage.scad]
2018-02-11 Tolerances, motor opening & clearance
    [z-axis-bottom.scad, z-axis-top.scad]
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2018-04-26 Older type of heatbed cover without screw holes
    [heatbed-cable-cover-no-screw.scad]
2018-07-17 Heatbreak and print cooling update
    Extruder body and cover : Improved cooling of the heatbreak by redesigning intake / outtake of cooling air with additional air feed opening. Improved PTFE tube holder for better flex materials handling. Nozzle fan : fan mounted at 45 degree angle to improve air flow, redesigned nozzle.
    [extruder-body-v2.stl, extruder-cover-v2.stl, nozzle-fan-45deg-support.stl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]
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2018-08-01 Heatbreak and print cooling update
    Heatbreak and print cooling update, removed second unused screw, cables clearance
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2018-09-27 heatbed cable clip for new Einsy_base (8mm sleeve)
    [Heatbed-cable-clip_for_8mm_sleeve.stl]
2018-09-27 nut holders edited, sleeve size changed to 6mm
    [heatbed-cable-cover-no-screw.stl]
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2018-09-27 tolerances changes
    [y-rod-holder.stl]
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2018-10-01 Older type of heatbed cover without screw holes (8mm sleeve)
    [heatbed-cable-cover_8mm_sleeve.scad]
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2018-10-01 Older type of heatbed cover without screw holes(8mm sleeve)
    [heatbed-cable-cover-no-screw_8mm_sleeve.scad]
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2019-07-25 Reinforced fin and PINDA holder
    Reinforced fin at the bottom of the heatsink and PINDA holder to avoid melting when printing with higher temperatures.
    [extruder-body.stl, extruder-cover.stl]
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2021-06-08 R7 - x axis bearings / lcd window
    x-carriage linear bearings holder update
    LCD window frame adjustment
    [LCD-cover-ORIGINAL-MK3.scad, LCD-cover-ORIGINAL-MK3.stl, bearing.scad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]
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2022-11-14 Missing version info added
    [LCD-cover-ORIGINAL-MK3.scad, x-carriage-back.scad, x-carriage.scad]
